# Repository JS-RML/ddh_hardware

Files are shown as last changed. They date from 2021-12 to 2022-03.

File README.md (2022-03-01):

# Direct-Drive Hand

In this project, we have implemented a two-fingered 4-DoF direct-drive hand, inspired by the work ["Direct Drive Hands: Force-Motion Transparency in Gripper Design"](http://www.roboticsproceedings.org/rss15/p53.pdf). 

ddh

# Table of Contents

- [Preparation](#preparation)
  - [Bill of Materials (BOM)](#bom)
    - [Off-the-Shelf Parts](#purchase)
    - [3D Printing](#3d-printing)
  - [Install `ddh_driver`](#install-ddh-driver)
  - [Labeling Parts](#labeling-parts)
- [Actuators](#actuators)
  - [Actuator Assembly ⨉4](#assemble-actuators)
  - [Wiring](#wiring)
    - [Power Supply](#power-supply)
    - [Encoder Connection](#encoder-connection)
    - [Power Connection](#power-connection)
  - [Actuator Calibration](#actuator-calibration)
    - [Calibrate ODrives](#calibrate-odrives)
    - [Calibrate Zero Position](#calibrate-zero-position)
- [Gripper](#Gripper)
  - [Finger Assembly ⨉2](#finger)
  - [Gripper Assembly](#gripper-assembly)
  - [Mounting](#mounting-ur10)
  - [Validation](#validation)
- [Customization](#customization)
  - [Mounting](#custom-mounting)
  - [Geometry](#geometry)
  - [Fingertip](#fingertip)
- [Getting Started](#getting-started)

# Preparation

## Bill of Materials (BOM)

### Off-the-Shelf Parts

- [ODrive 3.6-56V](https://odriverobotics.com/shop/odrive-v36) ⨉2
- [T-Motor GB54-2](https://store.tmotor.com/goods.php?id=445) ⨉4
- [AS5048A Encoder + Diametrical Magenet](https://item.taobao.com/item.htm?id=619004953504) ⨉4
- [Bearing - outer-diameter = 10mm, inner-diameter = 6mm](https://item.taobao.com/item.htm?id=649671875461) ⨉12
- [Dowel Pin - diameter = 6mm, length = 10mm](https://detail.tmall.com/item.htm?id=522002486638) ⨉6
- [14-Core Shielded Cable TRVVSP4](https://detail.tmall.com/item.htm?id=649477061772) ⨉2 meters
- [MX1.25-6P 150mm Cable](https://item.taobao.com/item.htm?id=607231799768) ⨉4
- [AMASS Braided 3-Phase 90cm Cable](https://item.taobao.com/item.htm?id=520248392055) ⨉8
- Adapter Plate and Coupling: The gripper is primarily designed to be compatible with [Universal Robots UR10](https://www.universal-robots.com/products/ur10-robot/) (50mm PCD with 4 ⨉ M6, used with Robotiq's grippers). For other robot systems, see the section [Customization](#custom-mounting) for instructions.
- Various Fasteners from M2 to M4

### 3D Printing 

- [Magnet Holder](stl/magnet_holder.STL) ⨉4
- [Motor Plate](stl/motor_plate.STL) ⨉4
- [Proximal Link](stl/proximal_link.STL) ⨉4
- [Distal Link](stl/distal_link.STL) ⨉2
- [Distal Tip Link](stl/distal_tip_link.STL) ⨉2
- [Finger Tip](stl/finger_tip.STL) ⨉2
- [Gripper Shell](stl/gripper_shell.STL) ⨉1
- [Coupler](stl/coupler.STL) ⨉1
- [Calibration Stand](stl/calibration_stand.STL) ⨉4
- [Calibration Arm](stl/calibration_arm.STL) ⨉4

## Install `ddh_driver`

`ddh_driver` is our driver software that provides a user interface to the gripper hardware. To install, visit [here](https://github.com/HKUST-RML/ddh_driver).

## Labeling Parts

Labeling parts can facilitate assembly.

### Motors

Label the four motors with `R0`, `R1`, `L0`, `L1`, respectively. The motors will __not__ be interchangeable later.

### ODrive

Label the two ODrive boards with `ODrive_R` and `ODrive_L` respectively. Record their serial numbers in `ddh_driver/config/default.yaml`. You can check the serial number using `odrivetool` in the terminal.

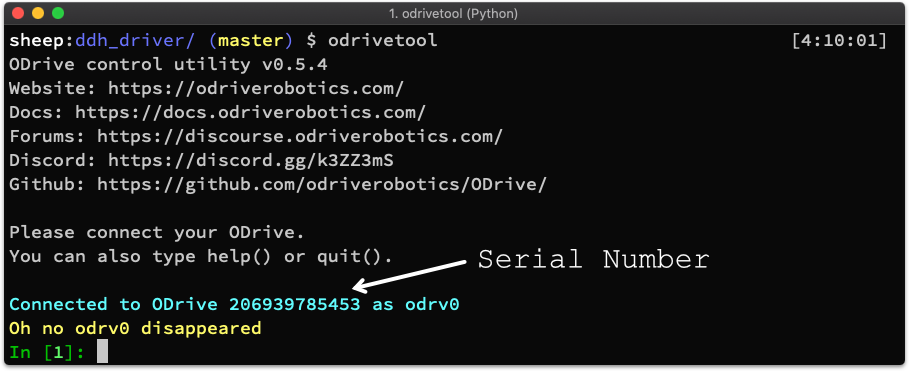
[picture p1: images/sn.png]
sn


```yaml
odrive_serial:
  R: 'Serial Number of ODrive_R'
  L: 'Serial Number of Odrive_L'
```

### Gripper Shell

On one side of the 3D-printed part `Gripper Shell` (to be used as the top side), mark reference frames as follows.

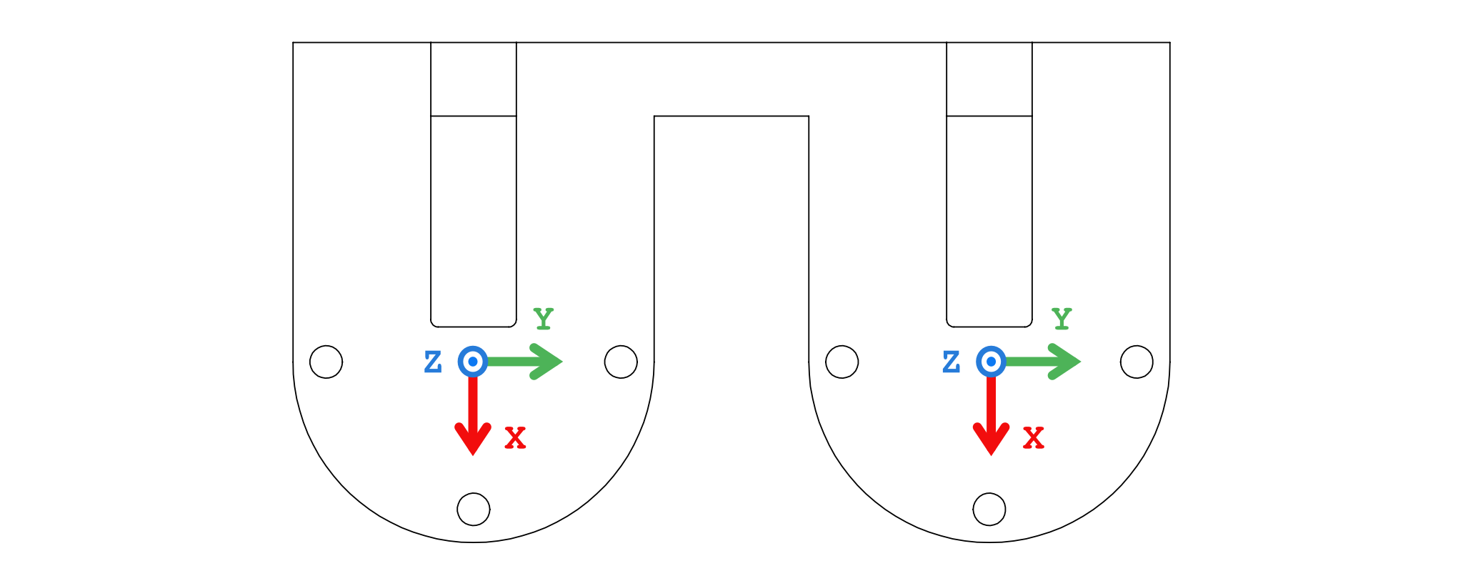
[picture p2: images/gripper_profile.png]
ref_frame


# Actuators

Actuator = BLDC Motor + Magnet + Encoder + Drive Board

## Actuator Assembly ⨉ 4

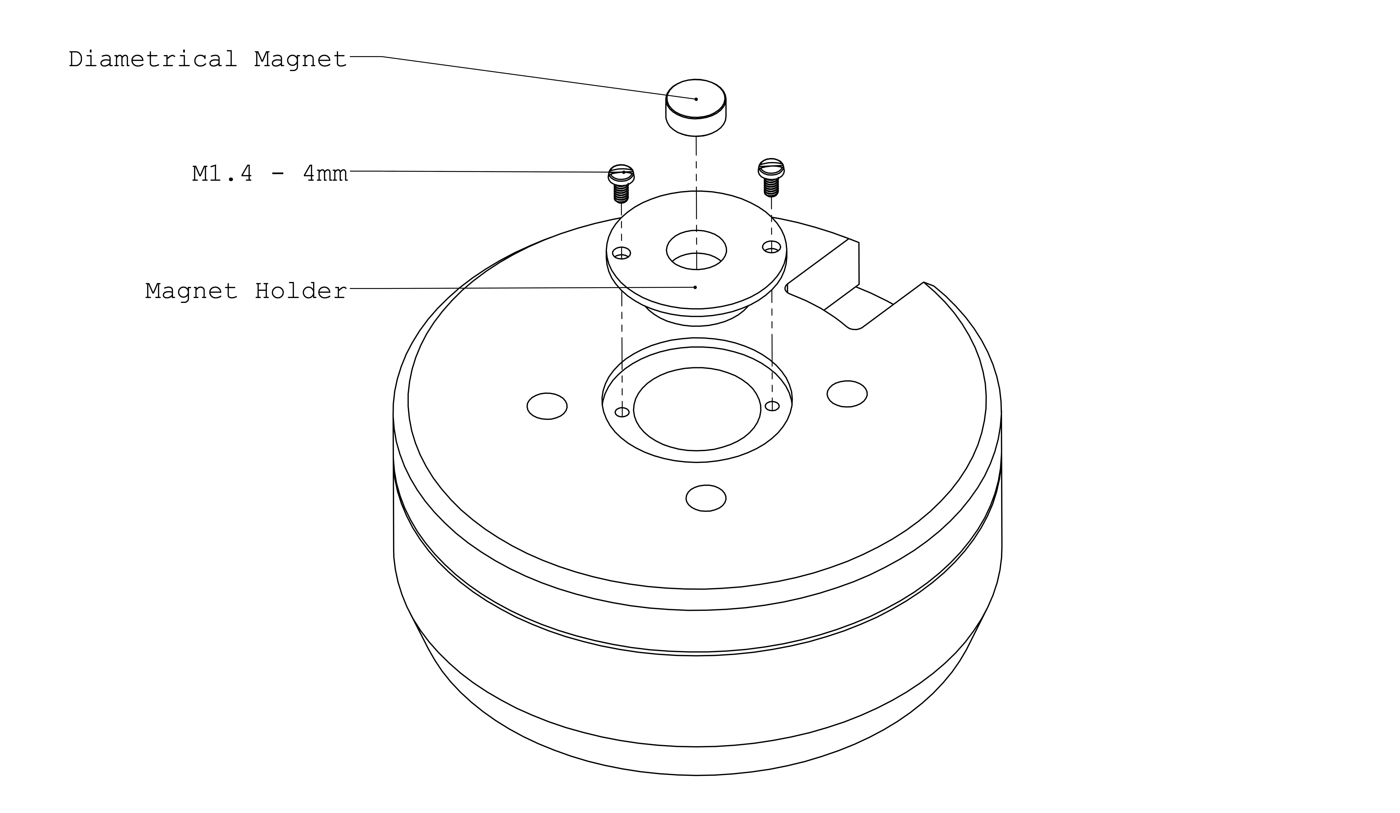
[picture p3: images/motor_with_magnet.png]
motor_with_magnet


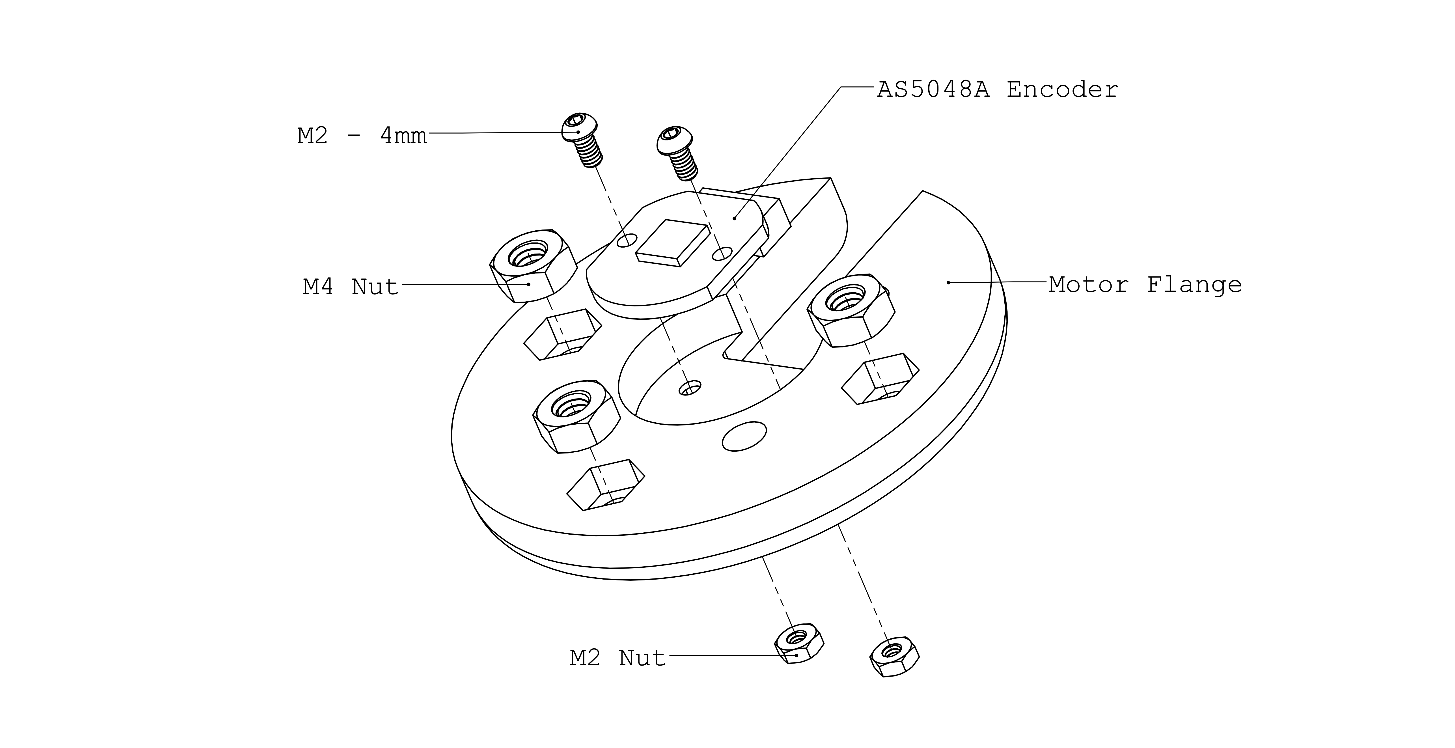
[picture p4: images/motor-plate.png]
motor-plate


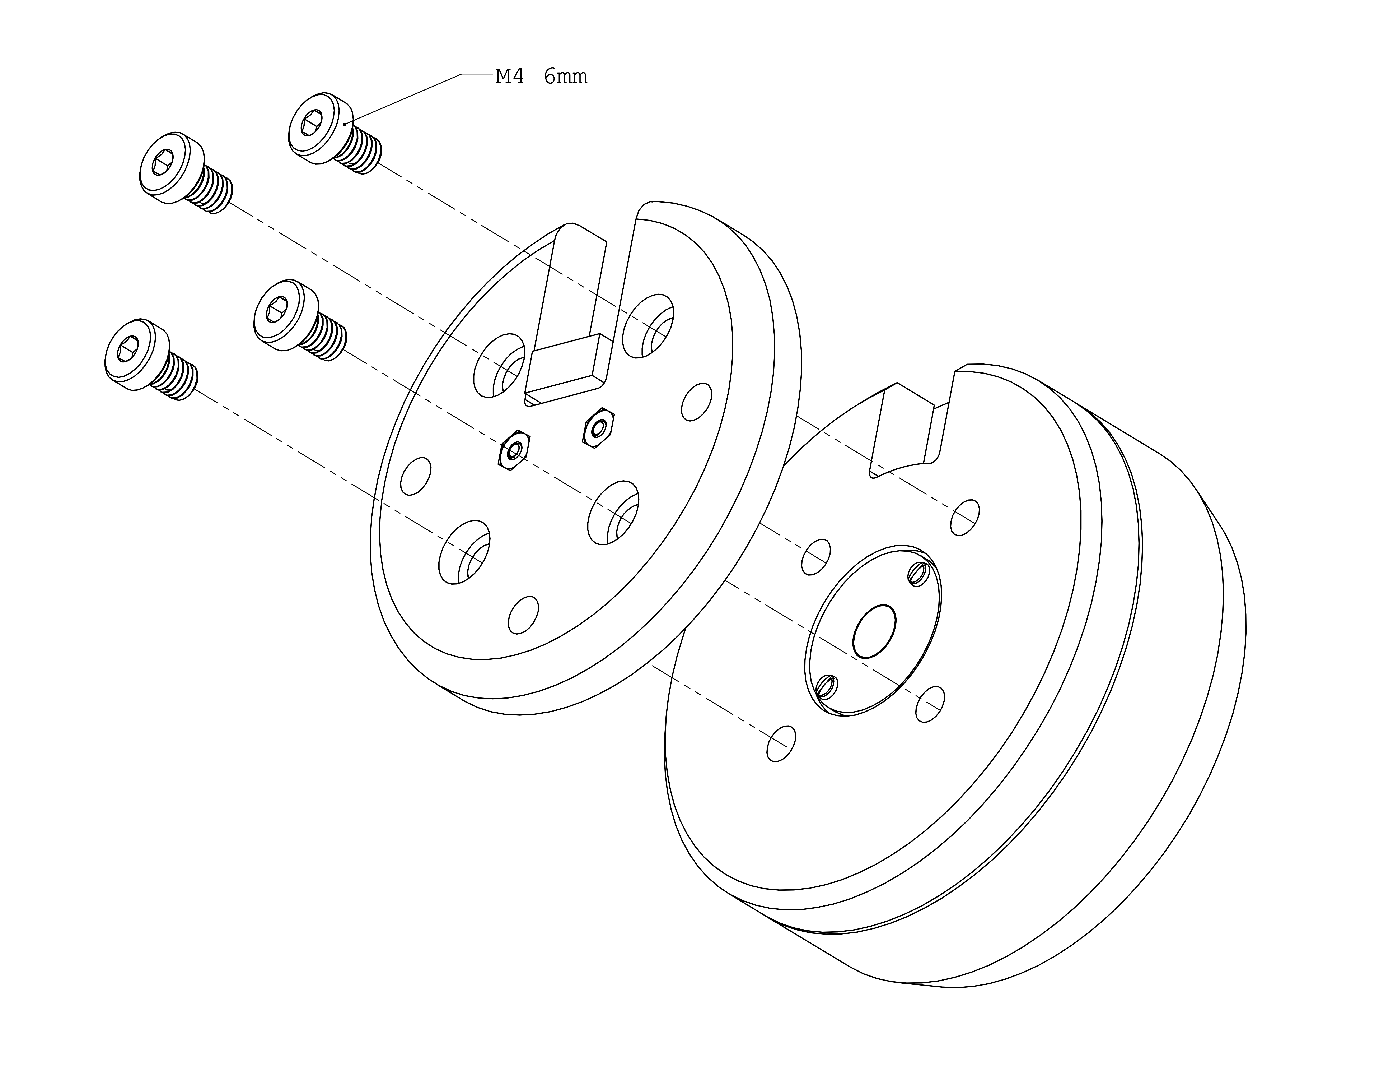
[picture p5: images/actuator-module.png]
actuator_module


## Wiring

The components should be connected following the diagram below. The encoder connection (black) and power connection (green) will be further elaborated.

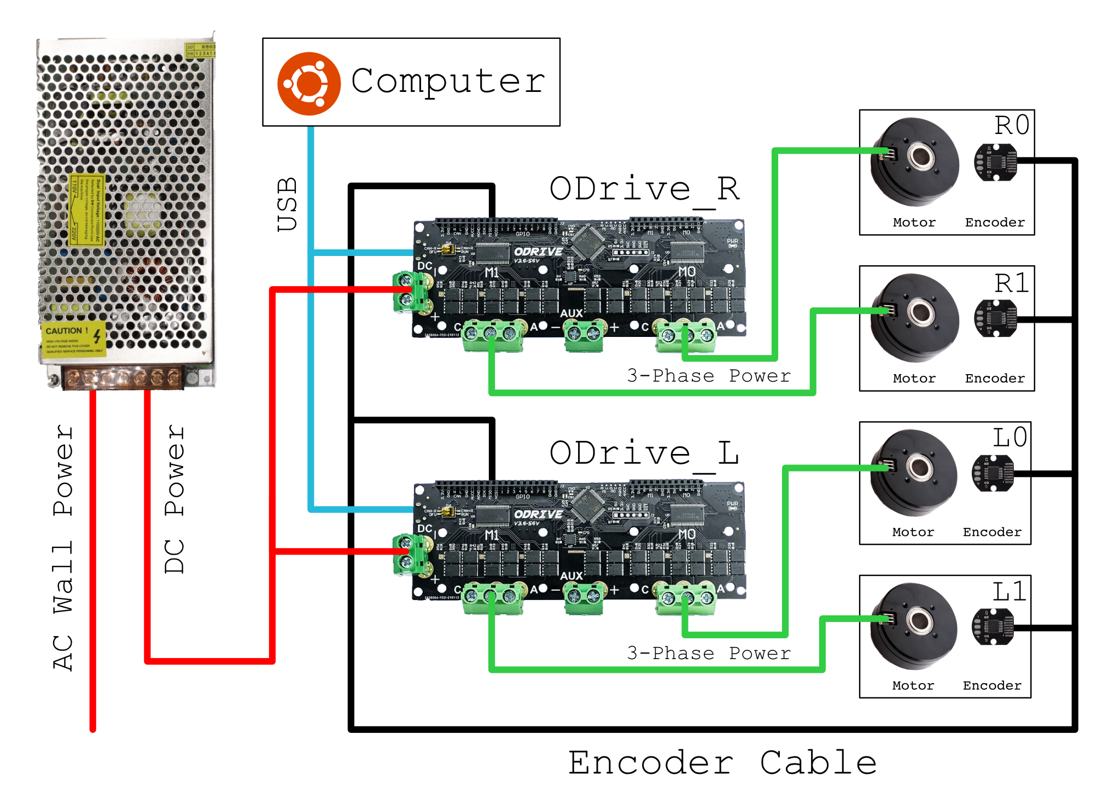
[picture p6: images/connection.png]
connection


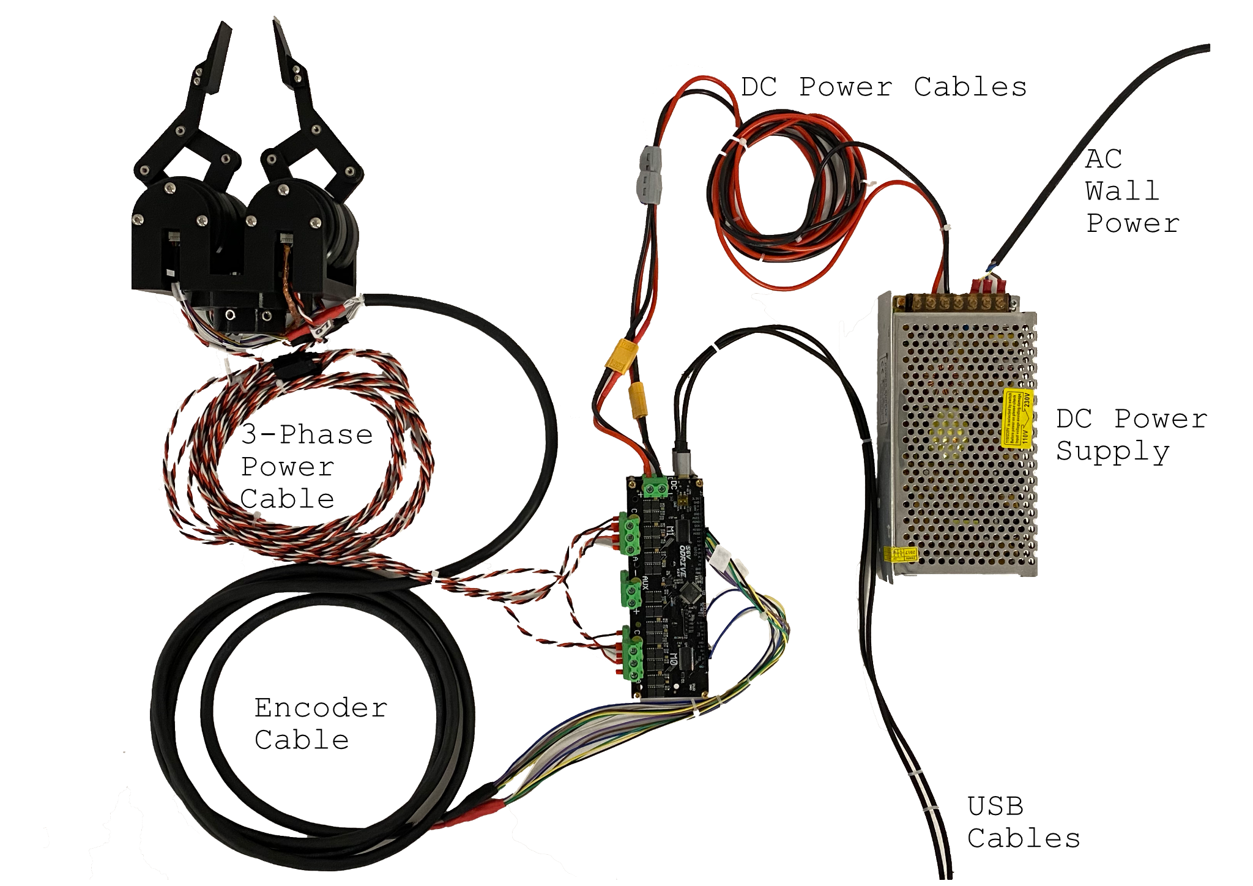
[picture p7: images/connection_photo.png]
connection_real


### Power Supply

First connect the DC power supply to the wall plug. The __brown__, __blue__, and __yellow__ wires correspond to __L__, __N__ and __Ground__ ports on the power supply. Then connect it to the two ODrive boards, positive to positive, negative to negative. There is no on/off button, plug in the wall plug to turn the system on, unplug to turn it off. Power it on does not arm the motors.

### Encoder Connection

For the encoder connection, we fabricate a cable assembly as shown below in the schematic. It is recommended to verify the connectivity and resistance of each connection to make sure the cables are soldered properly. We also recommend to label each connector like the schematic.

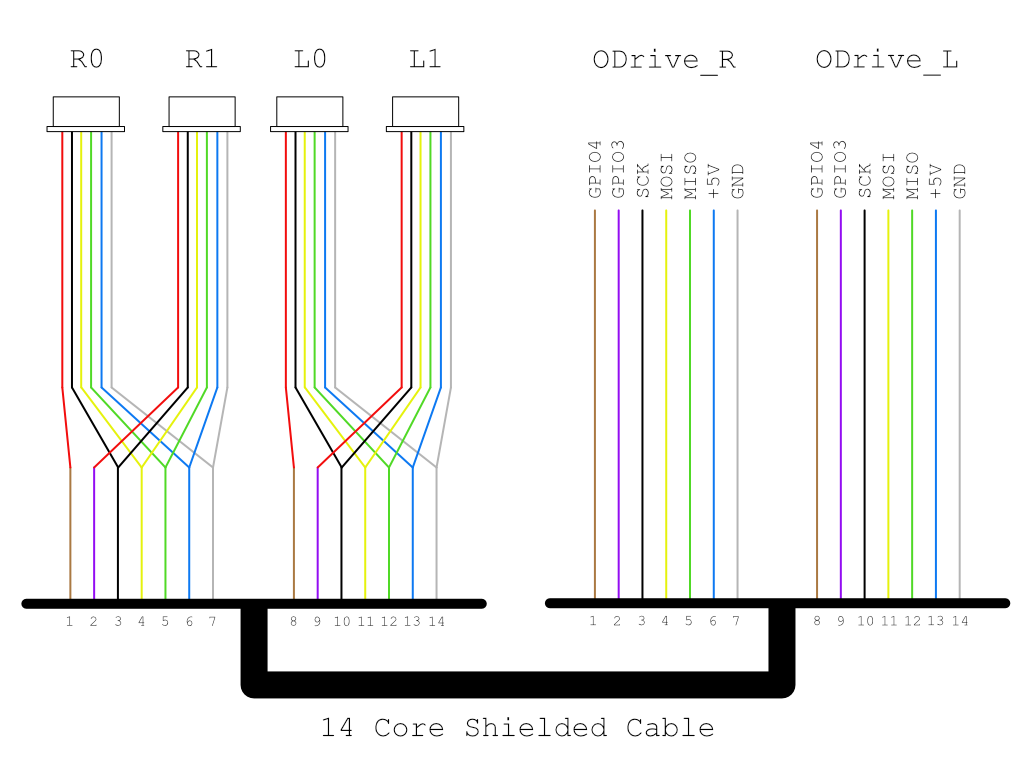
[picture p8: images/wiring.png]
drag_cable


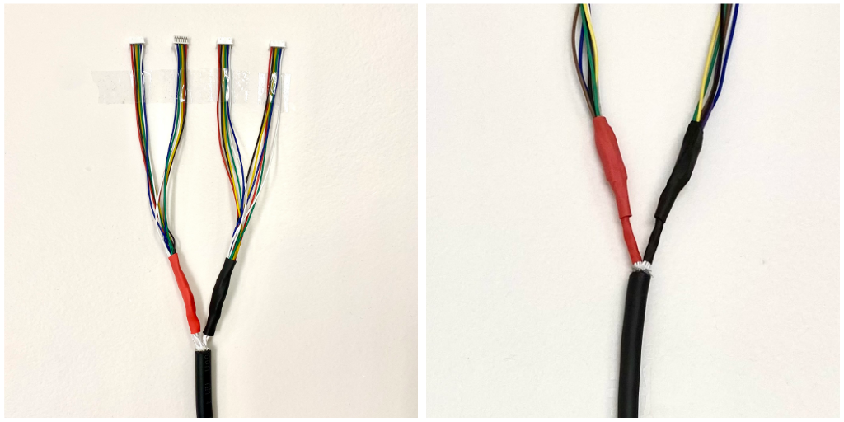
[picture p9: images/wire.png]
wire


After successful fabrication, connect the motor encoders and the ODrives.

### Power Connection

For the power connection, the motors are matched with the ODrive axes as follows: 

| Actuator | ODrive | Axis |
|----|---|-----|
| R0 | ODrive_R | M0 |
| R1 | ODrive_R | M1 |
| L0 | ODrive_L | M0 |
| L1 | ODrive_L | M1 |

Keep the 3-phase connection consistent as shown below. 

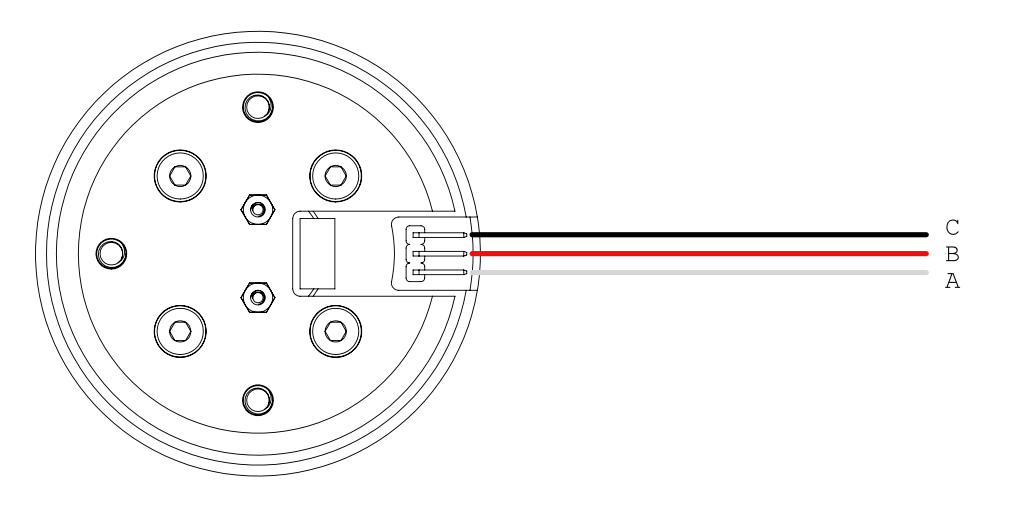
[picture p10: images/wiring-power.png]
wireing_power


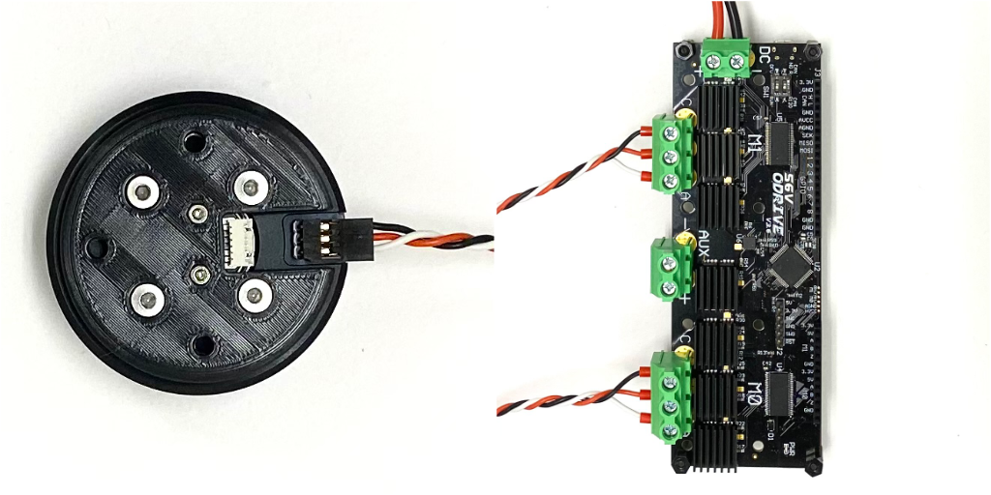
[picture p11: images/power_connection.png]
power-connection


## Actuator Calibration

Each actuator module require calibration before use. This step __can not__ be done after the gripper is assembled, so do not postpone this step.

We explicitly define the `direction of the rotor` to be the direction the hexagonal logo on the rotor is pointing at, and the `zero position of the motor` to be when the direction of the motor is pointing at the opposite direction of the power port on the stator. 

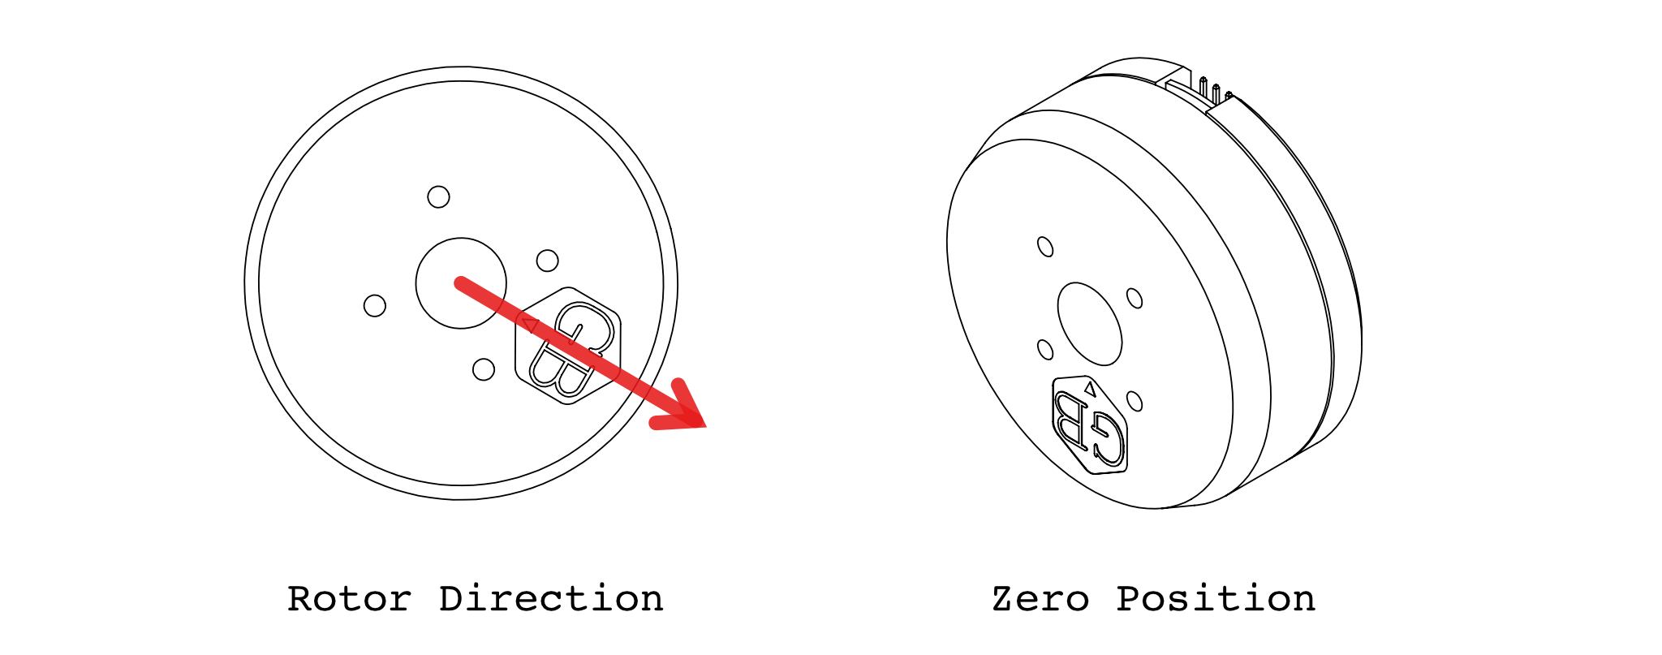
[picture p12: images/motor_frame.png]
motor-zero


### Calibrate ODrives

Execute the following command and follow its instructions in the terminal.

```shell
python3 -m ddh_driver.calib_odrive
```

### Calibrate Zero Position

Here we calibrate the zero position of the motor. Mount the actuator on the calibration stand and install the calibration arm onto the actuator according to the diagram

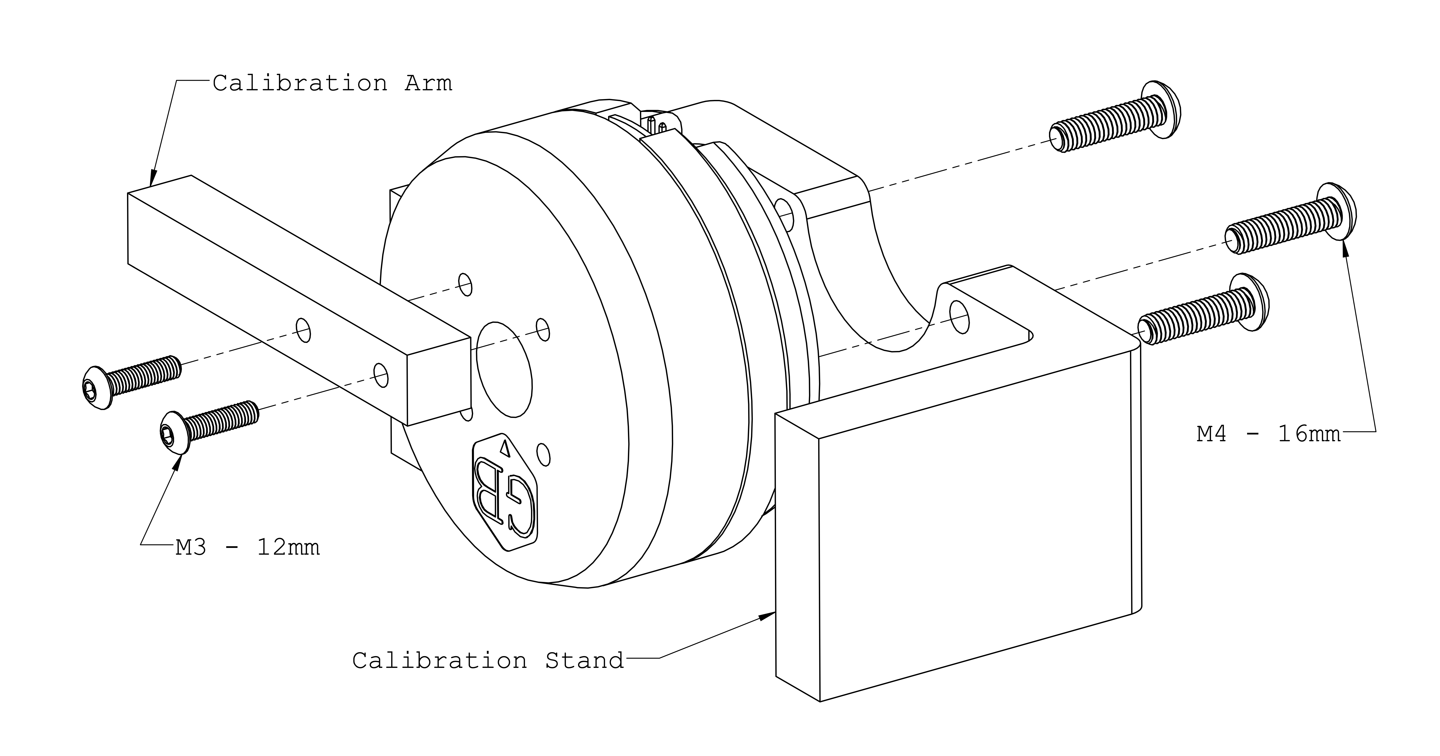
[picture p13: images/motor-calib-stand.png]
calibration-stand


Execute the following command to show real-time reading from the encoders.
```shell
python3 -m ddh_driver.check_encoder
```

Put the motor into zero position as show in the diagram below. Press down the calibration arm to make sure the stand and arm touch tightly. 

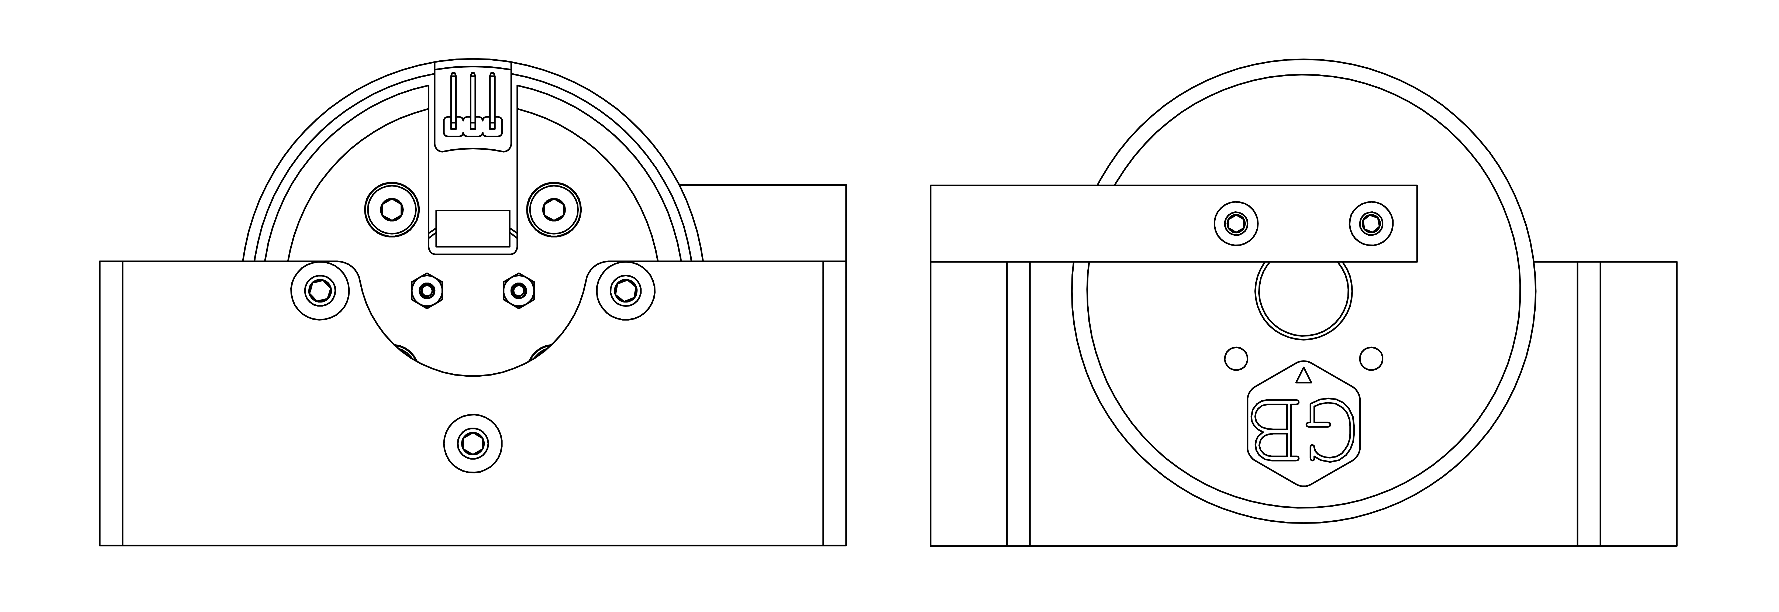
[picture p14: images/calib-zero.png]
zero-stop


Record the encoder reading in configuration in `ddh_driver/config/default.yaml`. Perform this calibration for each actuator and record it in their respective keys in the configuration file.
```yaml
motors:
  R0: # and R1, L0, L1:
    offset: the encoder reading at zero stop
```

After modifying the configuration file, execute the following command will show the real-time reading of the motor angular position in degrees.
```shell
python3 -m ddh_driver.check_motor_pos
```
It should be zero when motor is in [zero position](#zero-position-of-the-motor). Also try 90° and 180°. Don't mind the sign at this stage of assembly.

# Gripper

## Finger Assembly ⨉ 2

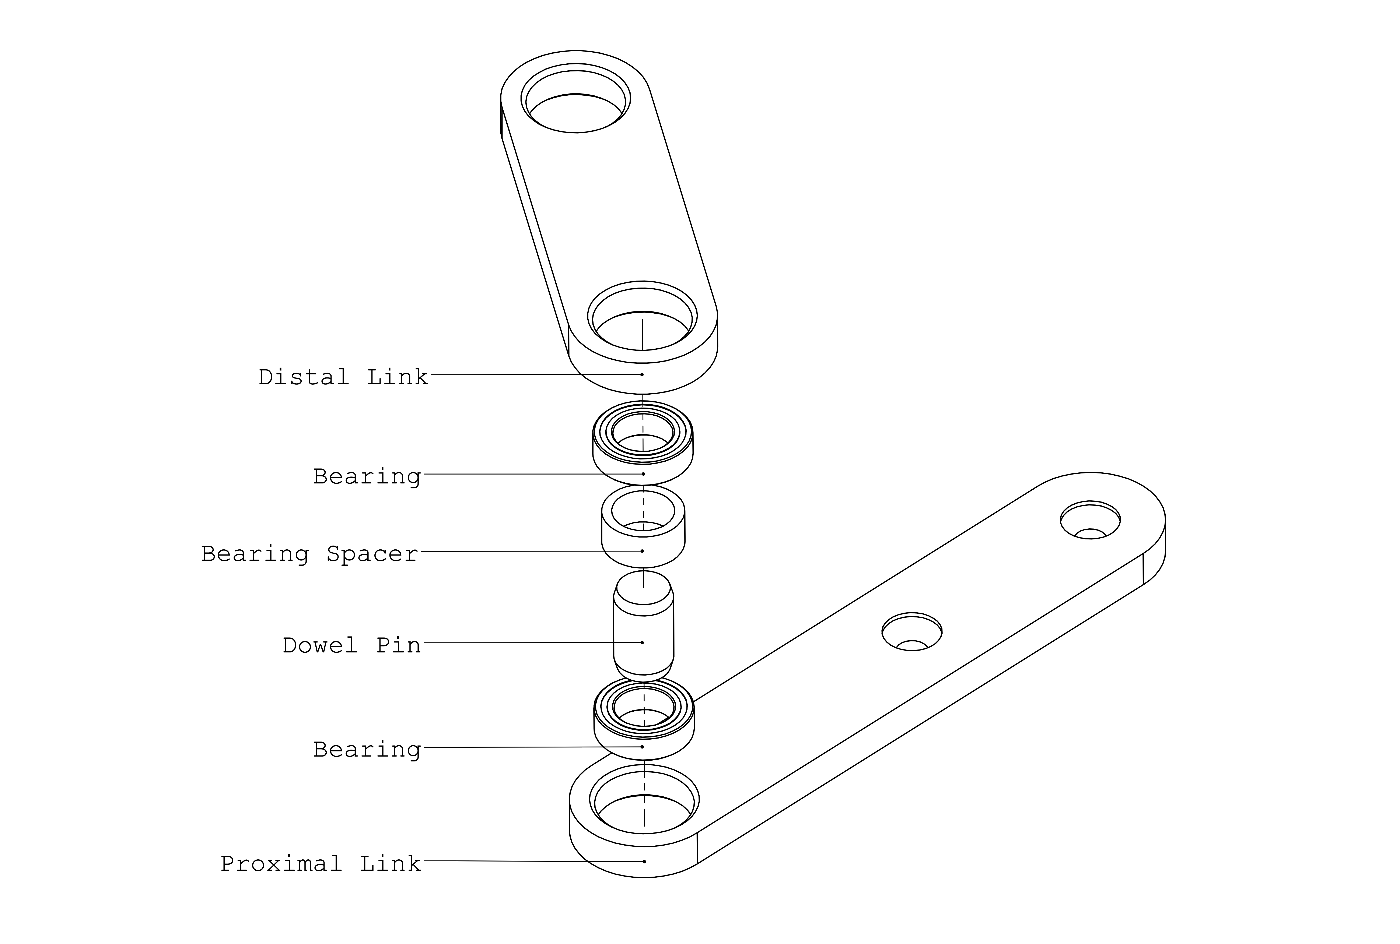
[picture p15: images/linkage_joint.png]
linkage_joint


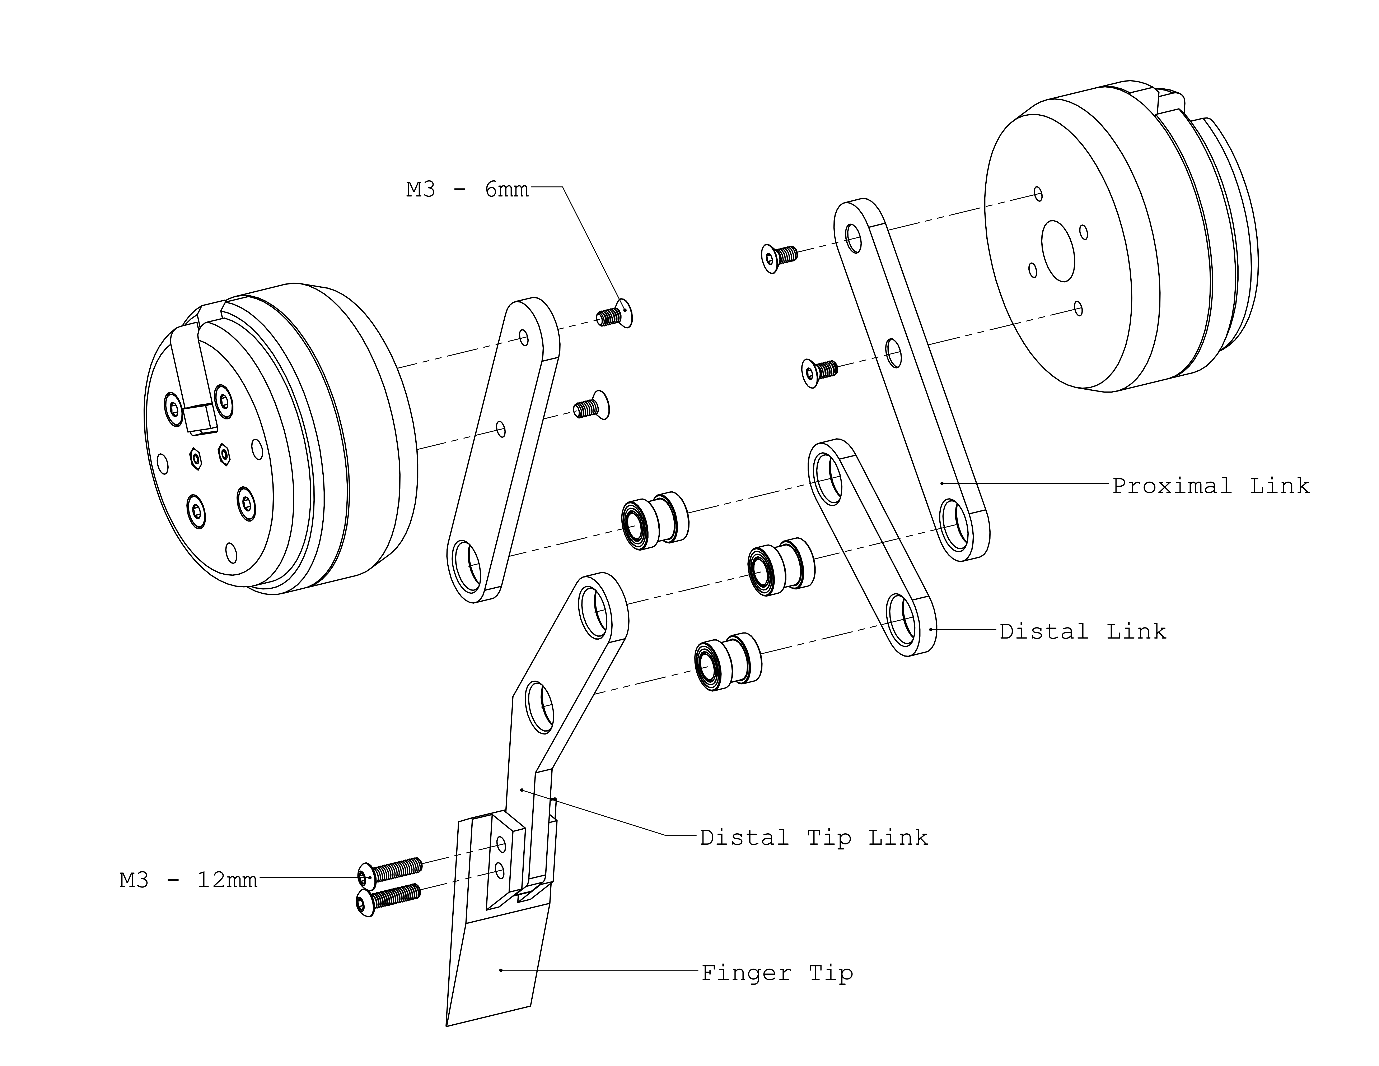
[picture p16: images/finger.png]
finger


## Gripper Assembly

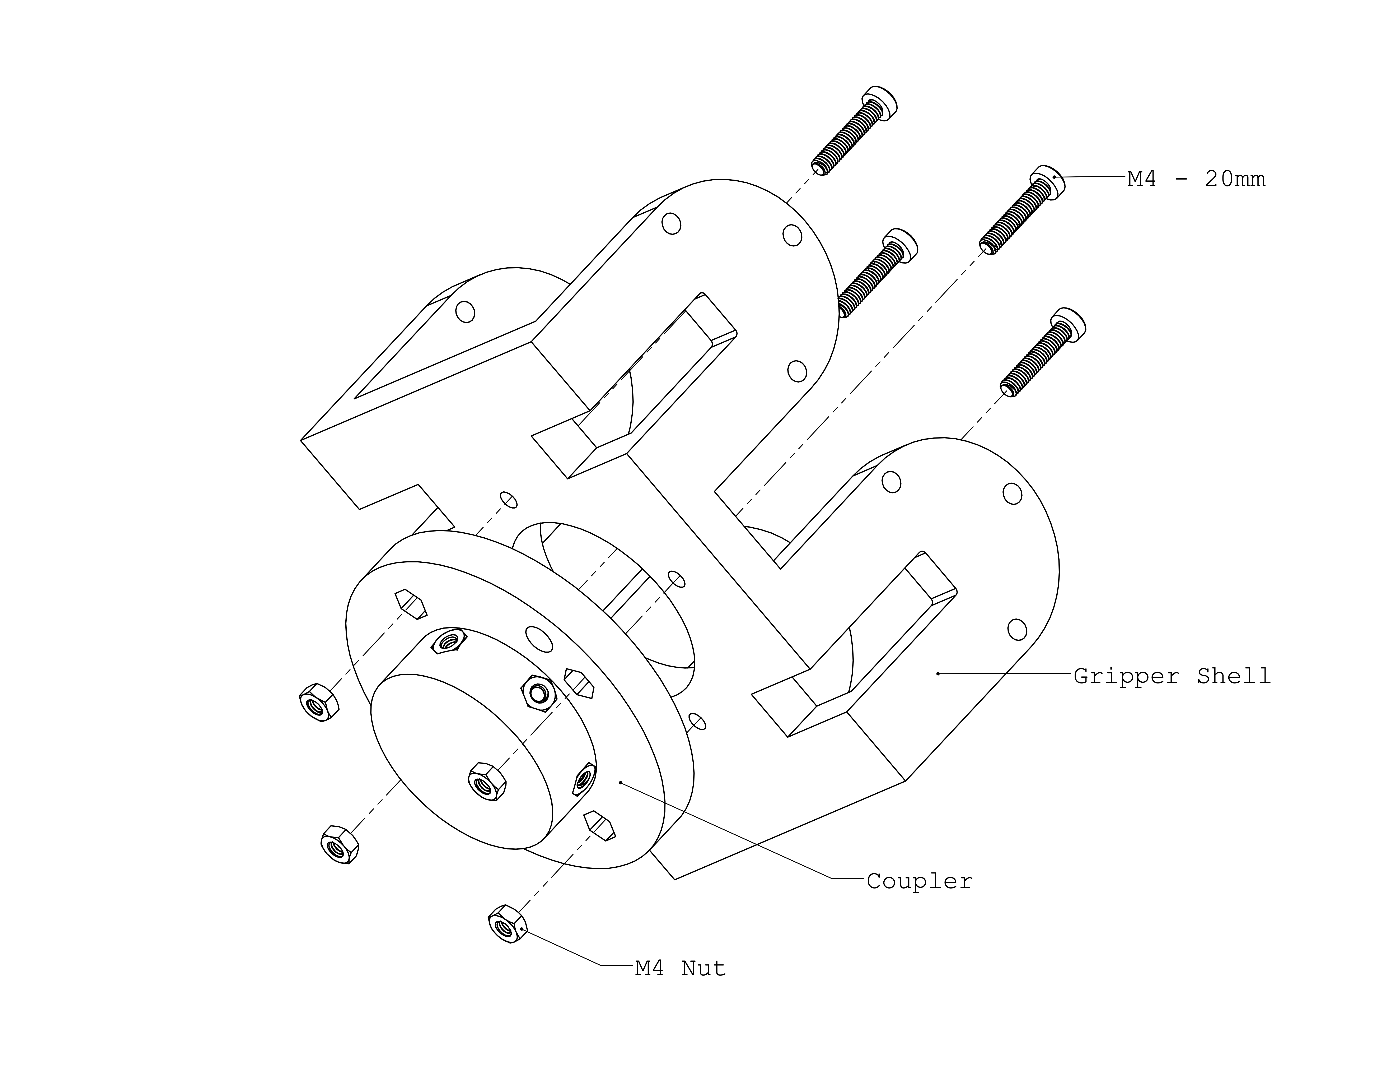
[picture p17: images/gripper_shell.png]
gripper_shell


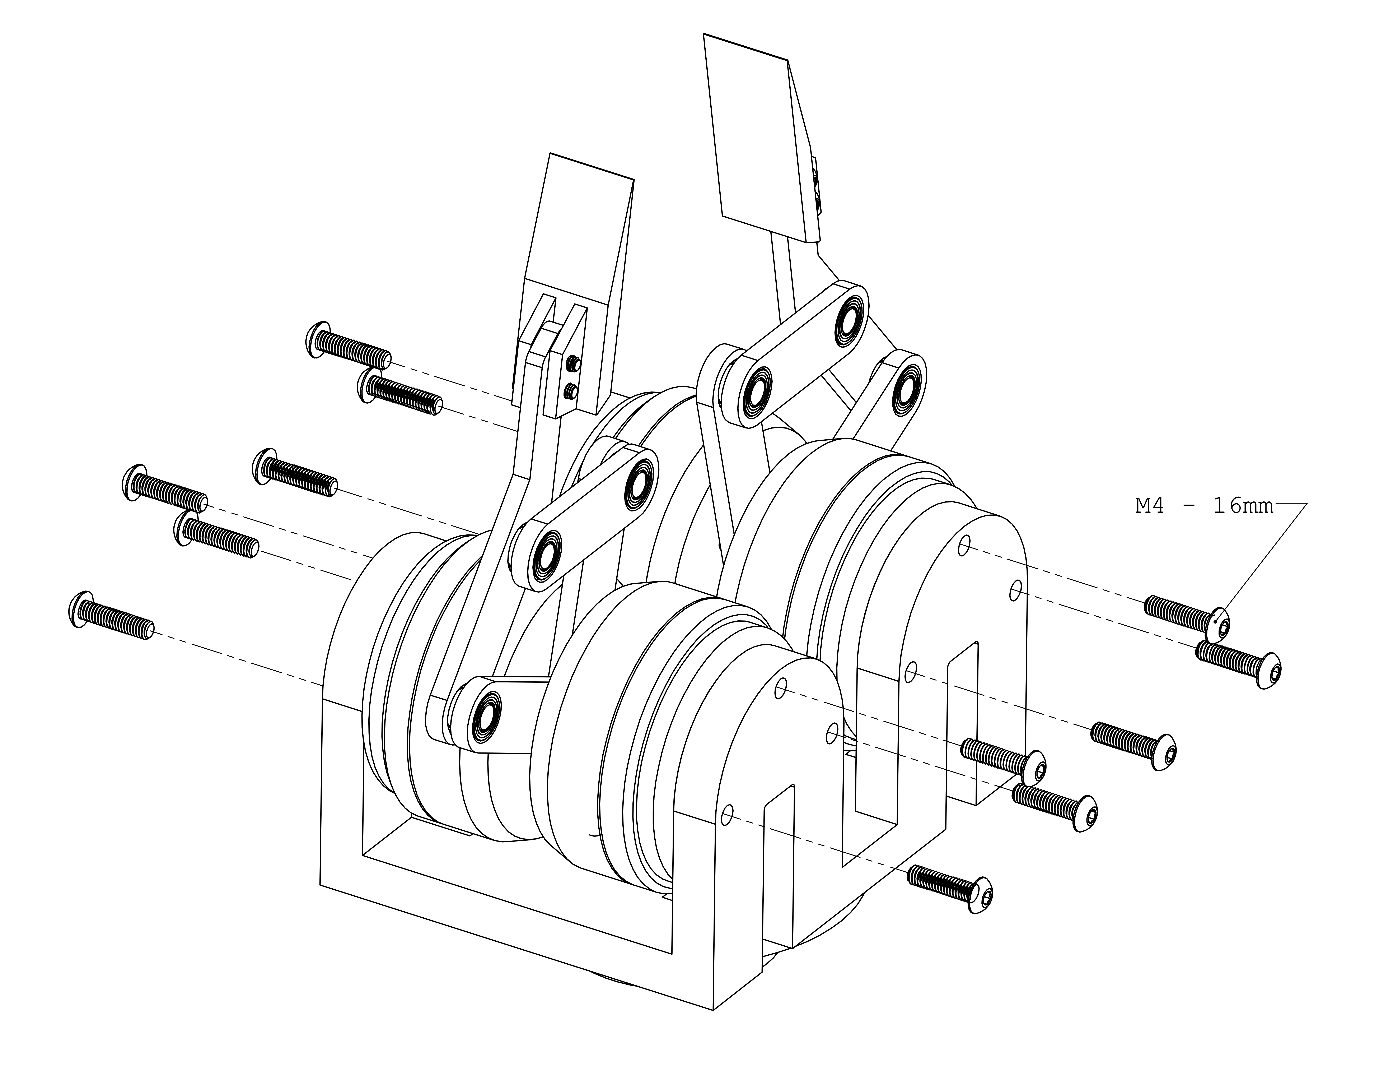
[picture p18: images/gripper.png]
gripper


## Mounting

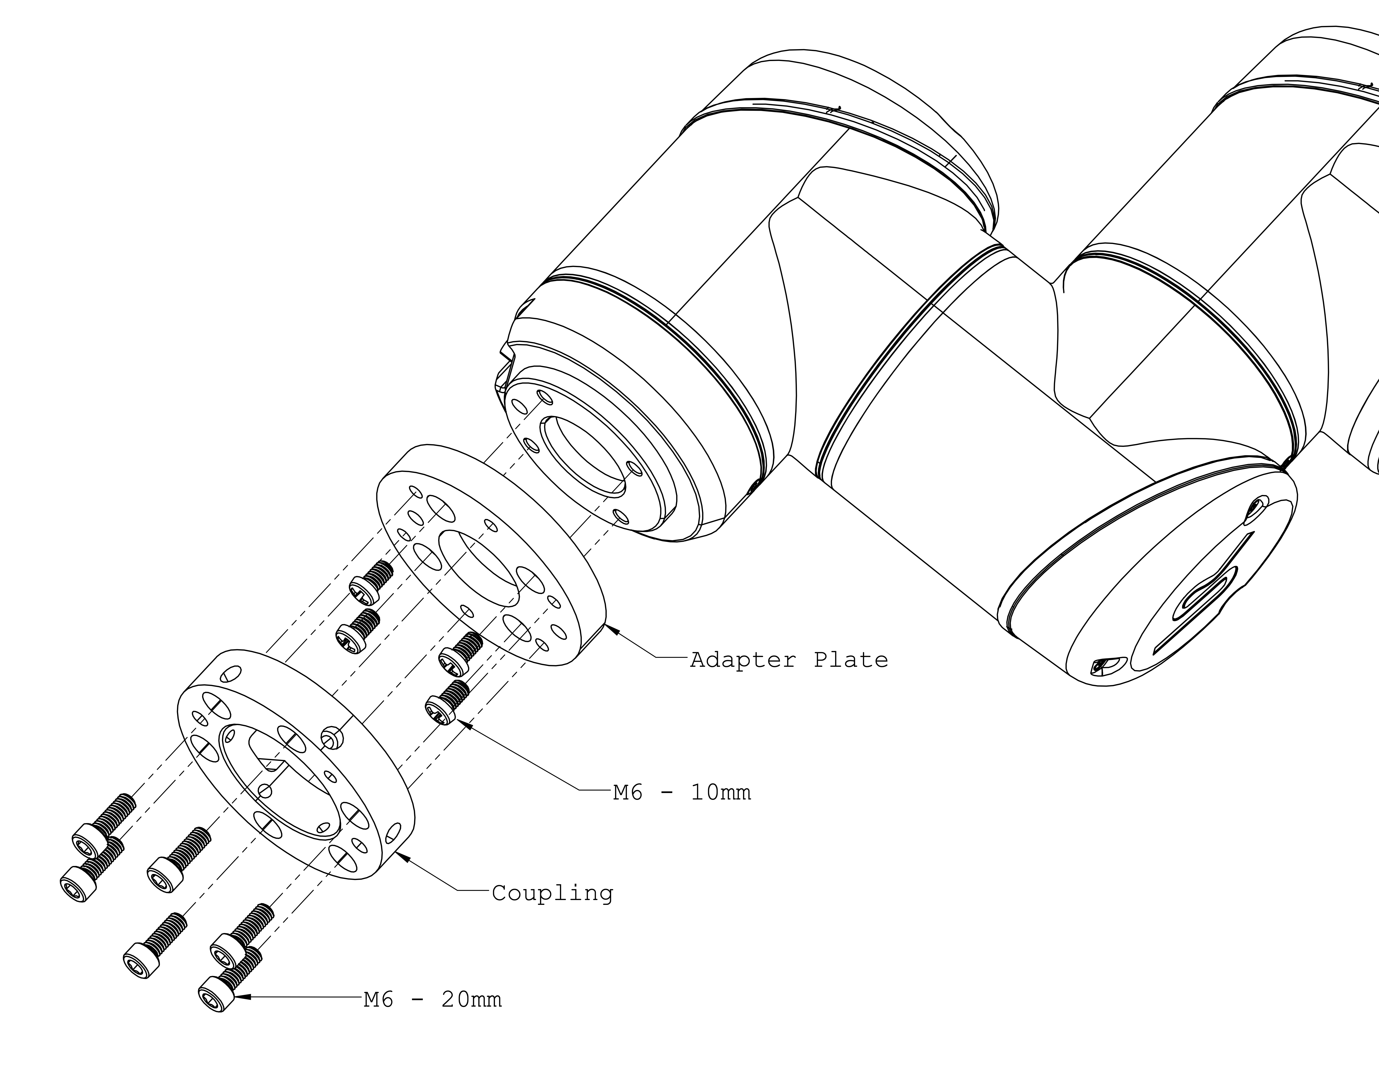
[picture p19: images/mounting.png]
mounting


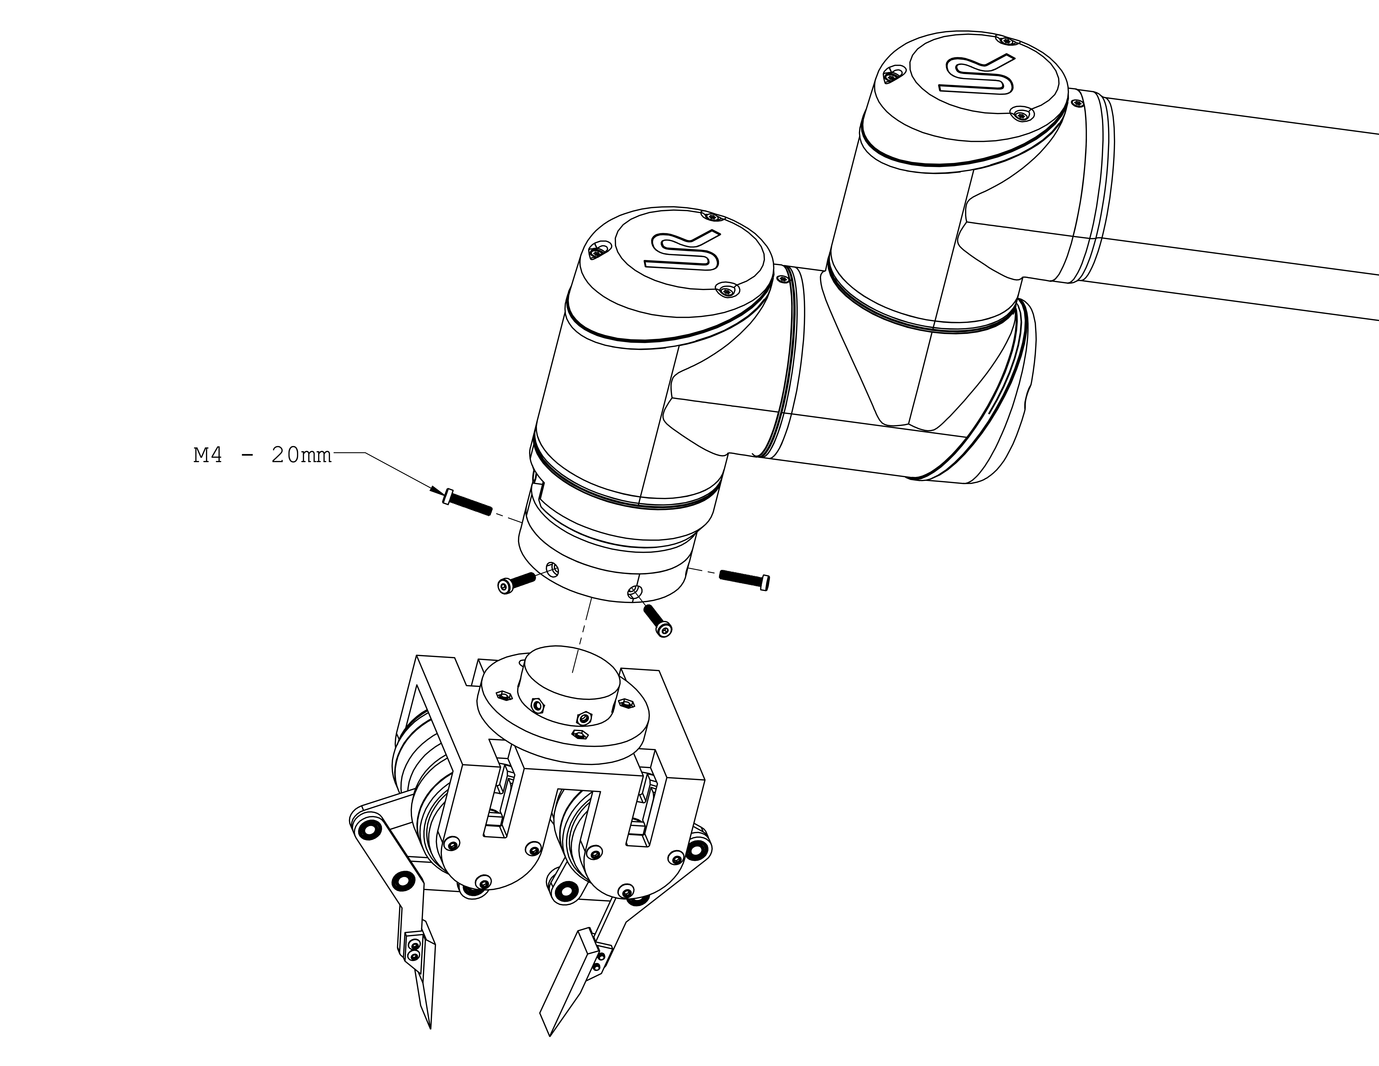
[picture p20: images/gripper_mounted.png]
gripper_mounted


## Validation

The gripper assembly is complete. Please perform the following validation steps to make sure the linkages and actuators are installed correctly.

First check the association between proximal links and actuators. They should follow the diagram below __exactly__. If there is a mismatch, please go back to the assembly steps and correct the mistakes.

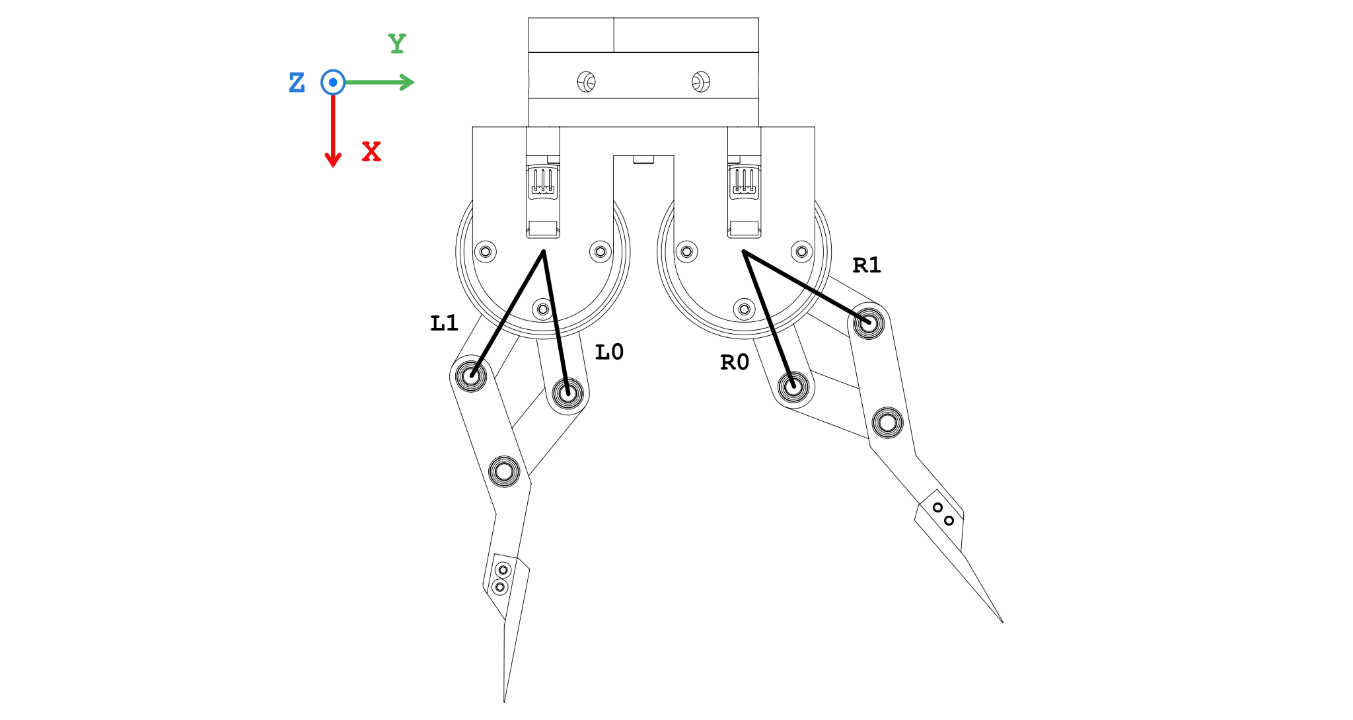
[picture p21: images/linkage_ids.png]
linkage_ids


Then check the angular position of the four proximal links. This value will be referred to as θ, with subscript indicating which link.  Execute the following command to print real-time reading of θ
```shell
python3 -m ddh_driver.check_theta
```
It should be the angle between the link and the x-axis, in counter-clockwise direction. For example, the following figure shows the angle of R0 link at -40°, 0°,  and 90°.
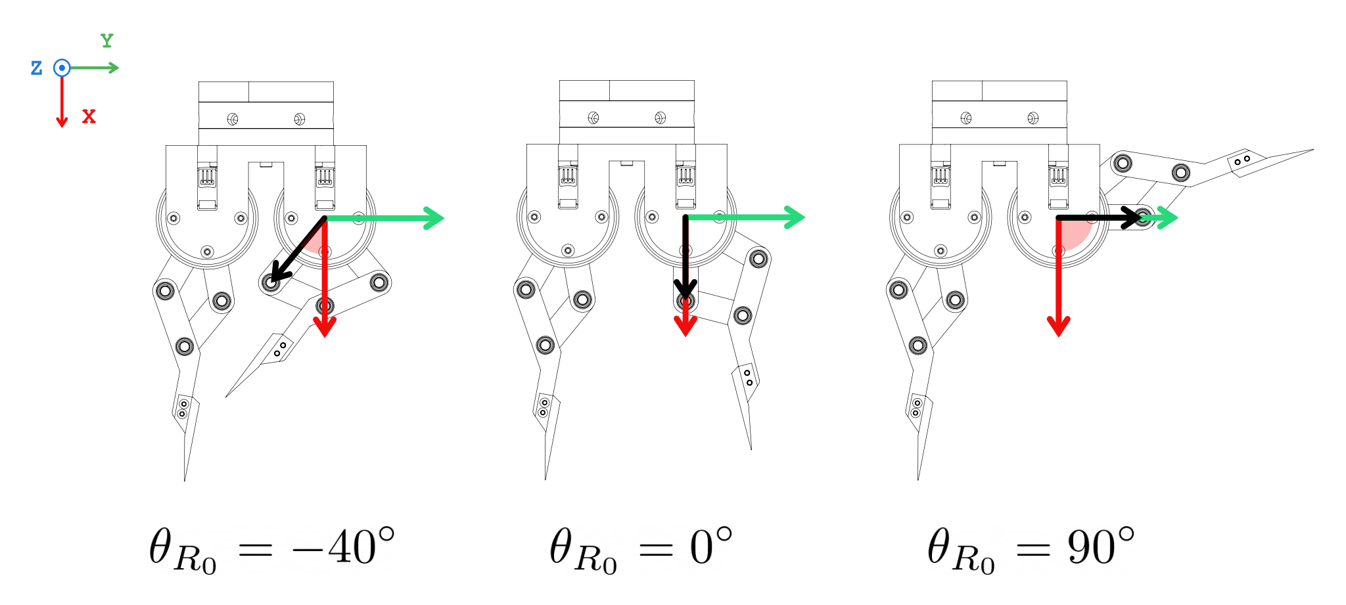
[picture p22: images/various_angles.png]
various-angles

If everything checked out at this point, you have successfully built and calibrated the direct-drive gripper.

# Customization

If the default setup does not satisfy your requirements, it can be further customized.

## Mounting

If the default mounting does not work for you, it's very easy to make a custom mount. The gripper has a __60 mm PCD with 4 ⨉ M4__ mounting interface, as shown in the drawing below.

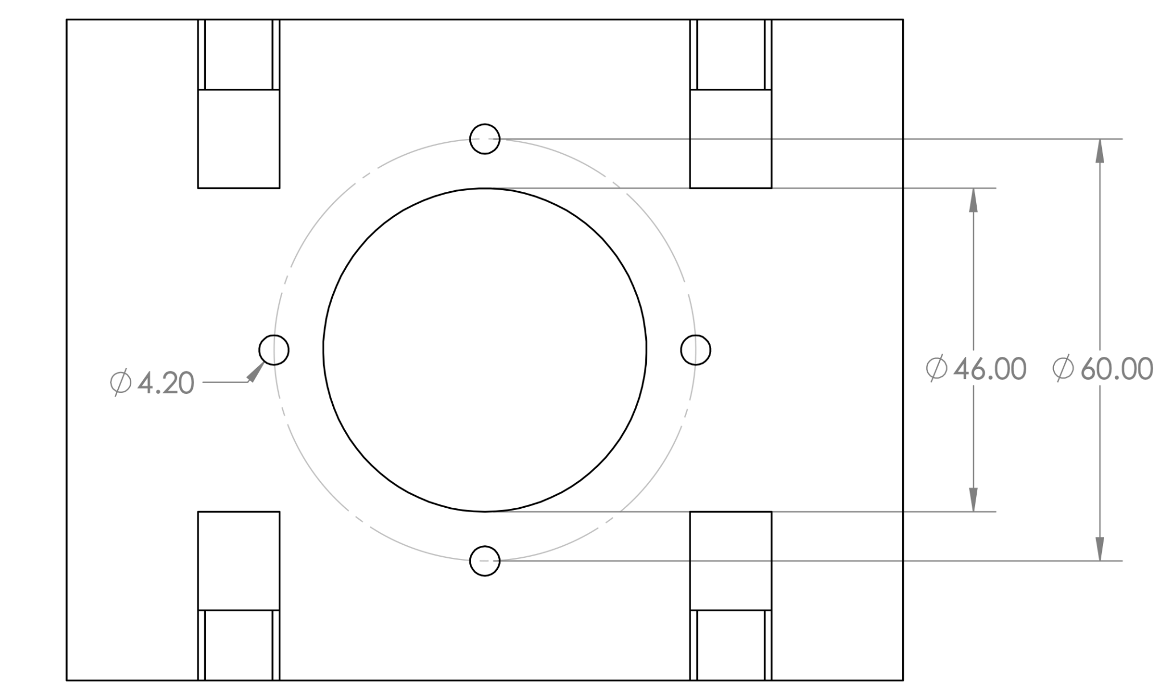
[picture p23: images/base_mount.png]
base_mount


## Geometry

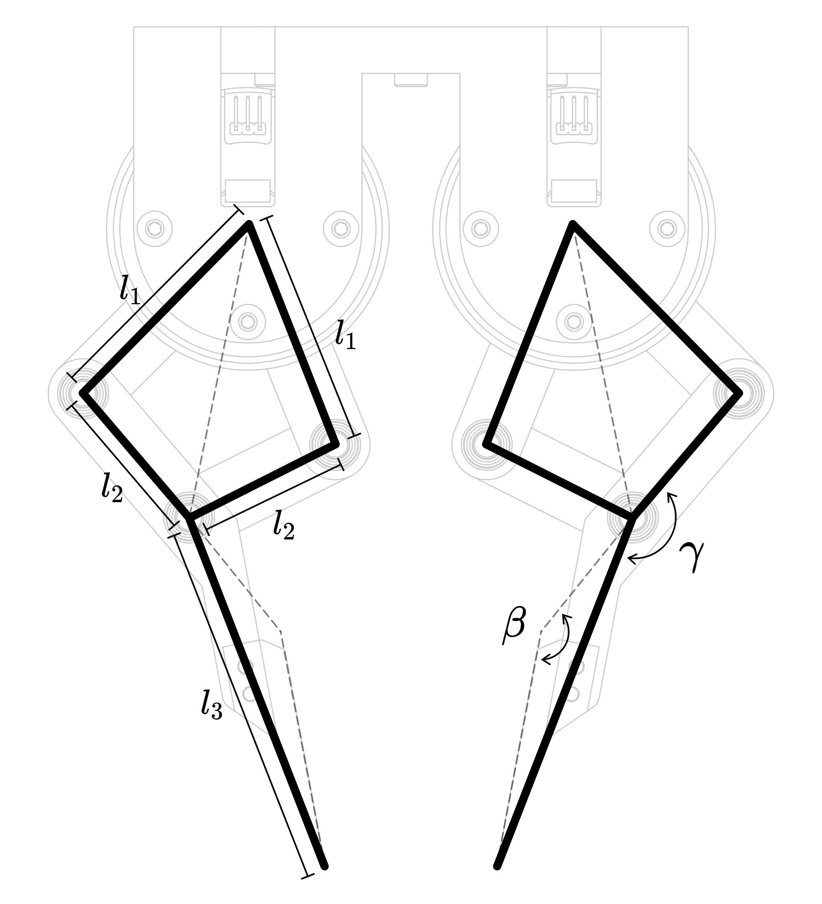
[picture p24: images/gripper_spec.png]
geometry


The geometrical parameters can be customized. After you design your custom parts, update the `ddh_driver/config/default.yaml` so the driver can work properly. 

| Parameter | Configuration Path | Unit |
|----|---|-----|
| ℓ₁ | `/geometry/l1` | mm |
| ℓ₂ | `/geometry/l2` | mm |
| ℓ₃ | `/geometry/l3` | mm |
| 𝝱 | `/geometry/beta` | degree |
| 𝛄 | `/geometry/gamma` | degree |

## Fingertip

The fingertip is designed to be swappable. It is attached to the distal link, shown in the schematic below. The default fingertip has a sharp tip for scooping thin objects. Customize the fingertip for your specific scenario. Beware that ℓ₃ and 𝝱 change with the fingertip geometry, make sure to update them in the configuration file.

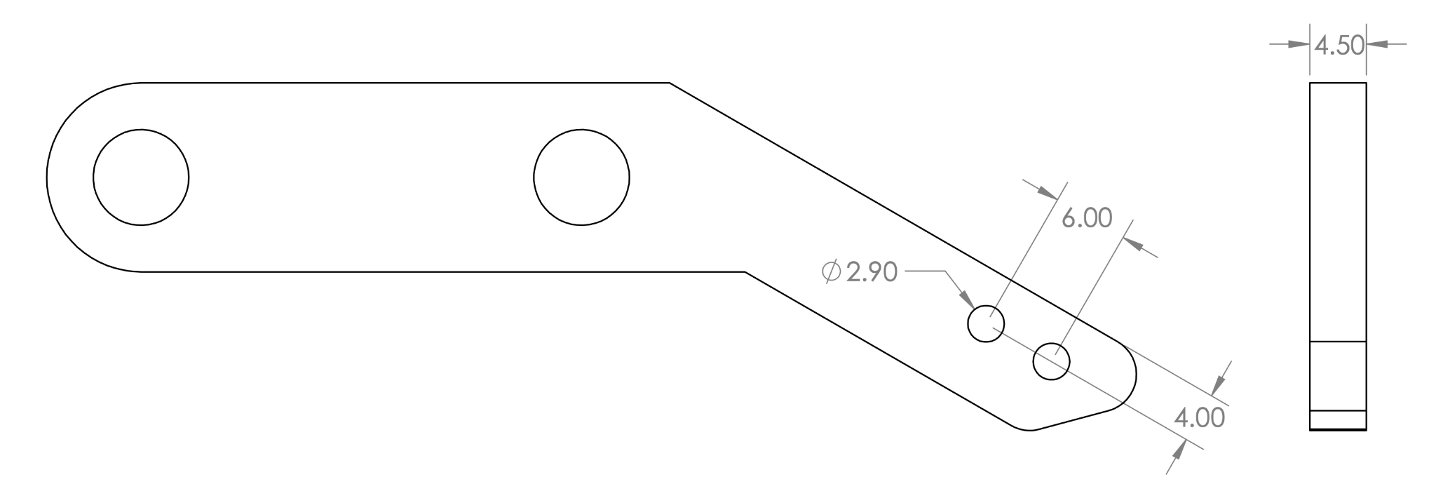
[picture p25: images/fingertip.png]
fingertip


# Getting Started

You have completed the assembly and calibration of the direct-drive gripper. To learn about how to use the gripper, please proceed to the [ddh_driver](https://github.com/HKUST-RML/ddh_driver) for tutorials and documentation.

# Maintenance

For any technical issues, please contact Pu Xu ([pxuaf@connect.ust.hk](mailto:pxuaf@connect.ust.hk))

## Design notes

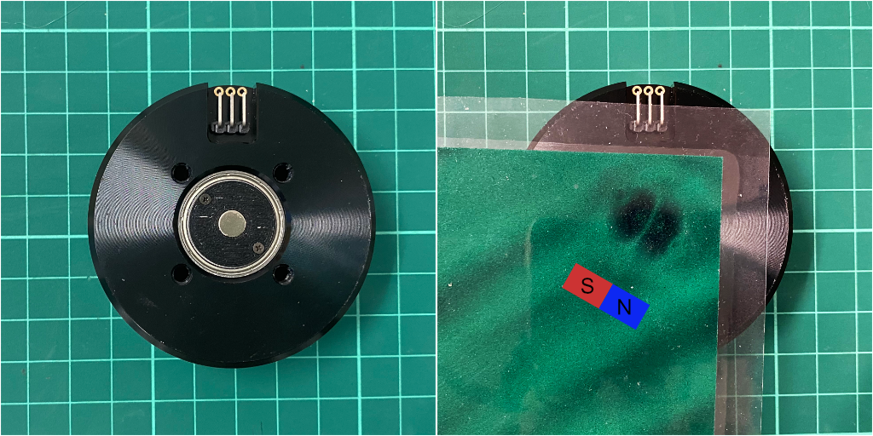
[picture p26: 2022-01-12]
images/magnet.png

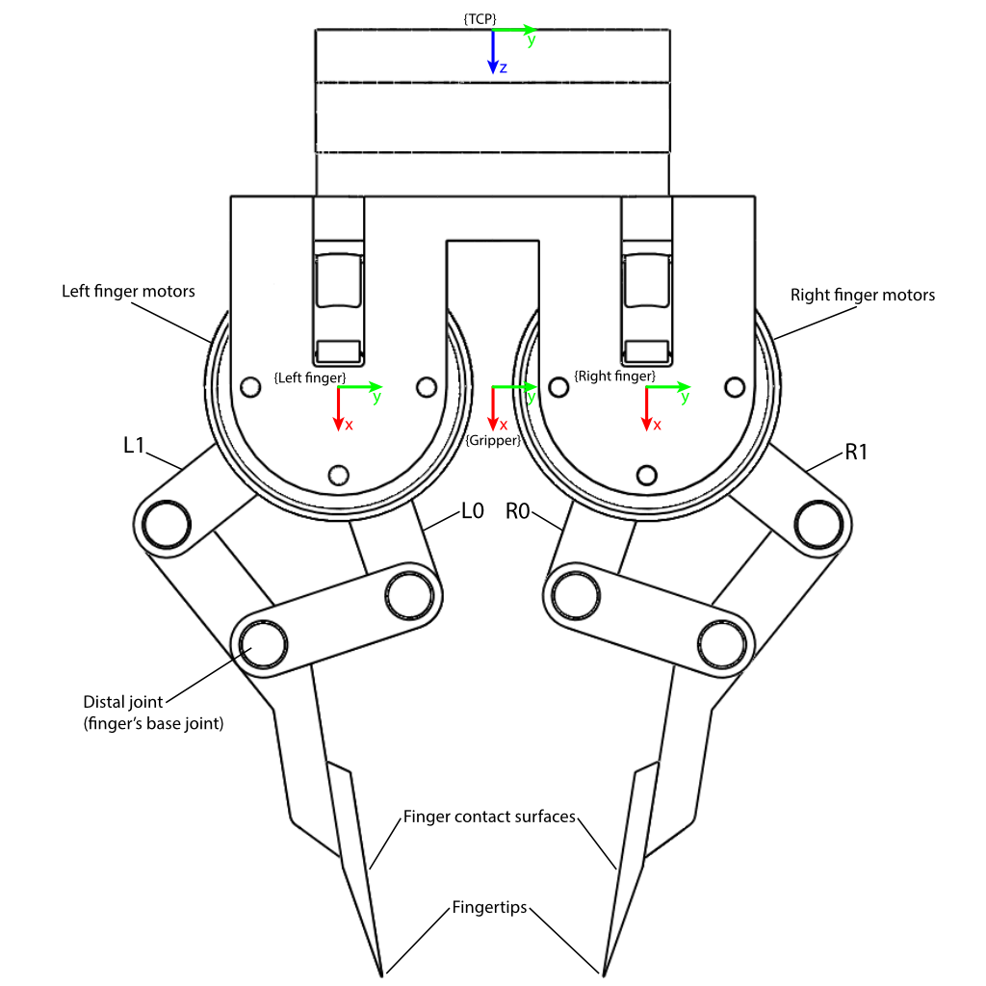
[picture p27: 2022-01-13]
images/ref_frame.png

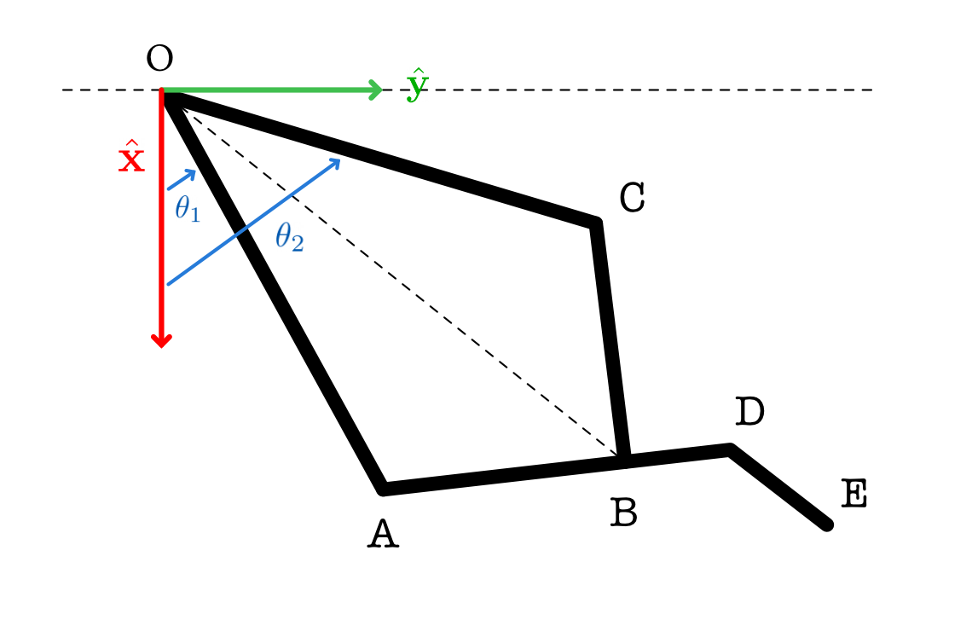
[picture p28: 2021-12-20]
images/theta1_theta2.png

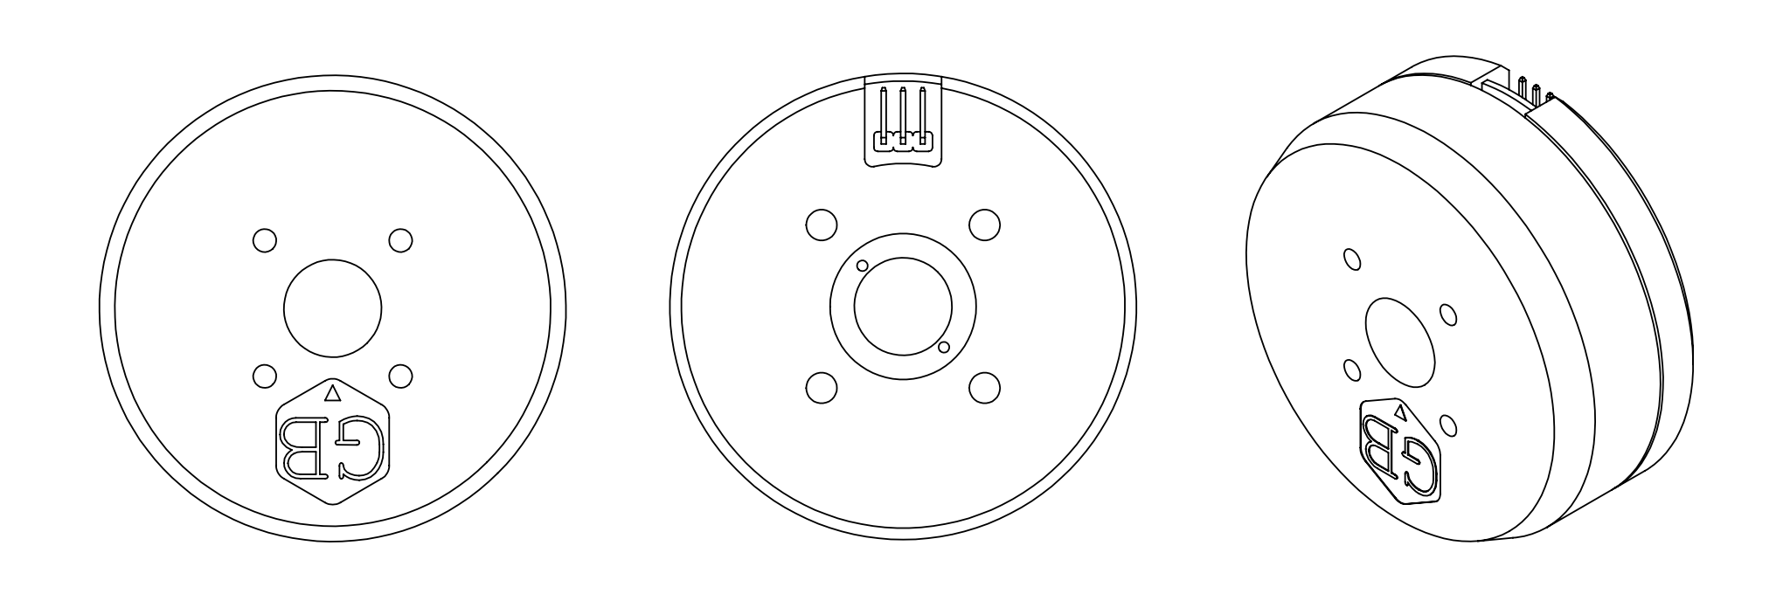
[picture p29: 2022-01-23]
images/motor_zero.png

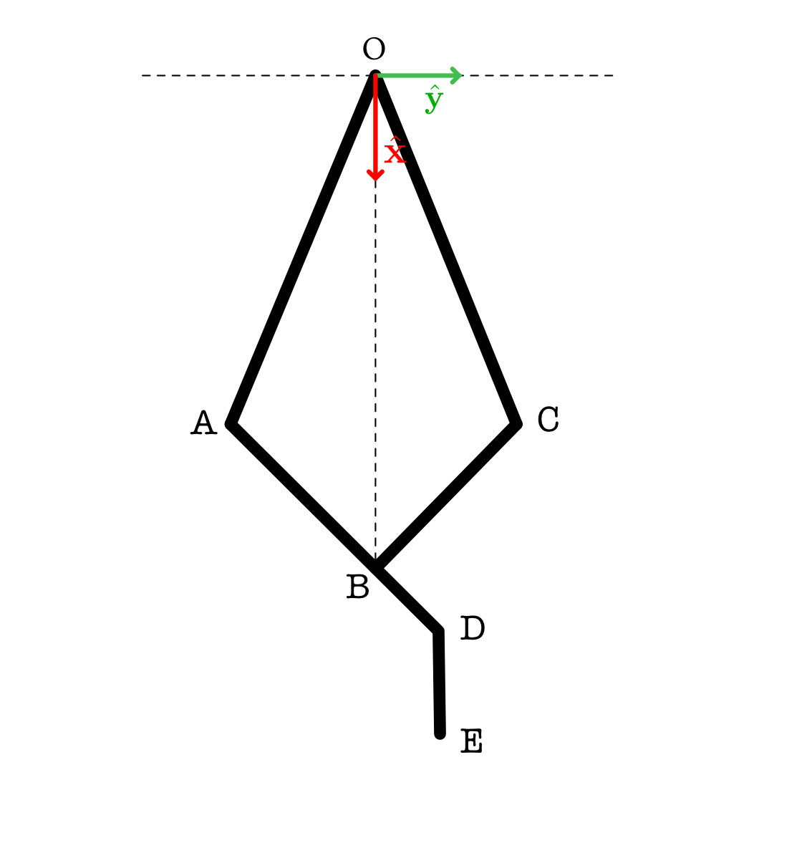
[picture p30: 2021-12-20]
images/linkage_geometry.png

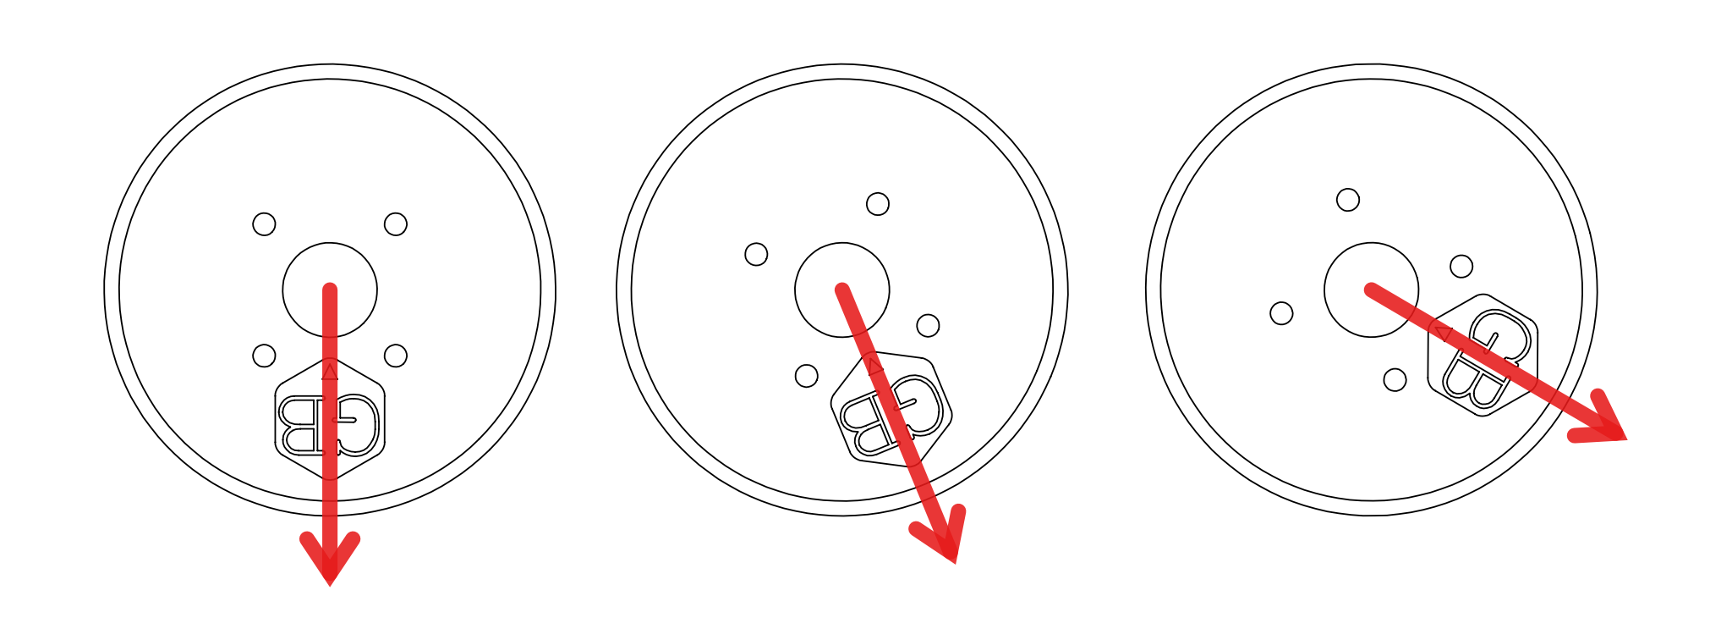
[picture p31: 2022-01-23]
images/rotor_dir.png

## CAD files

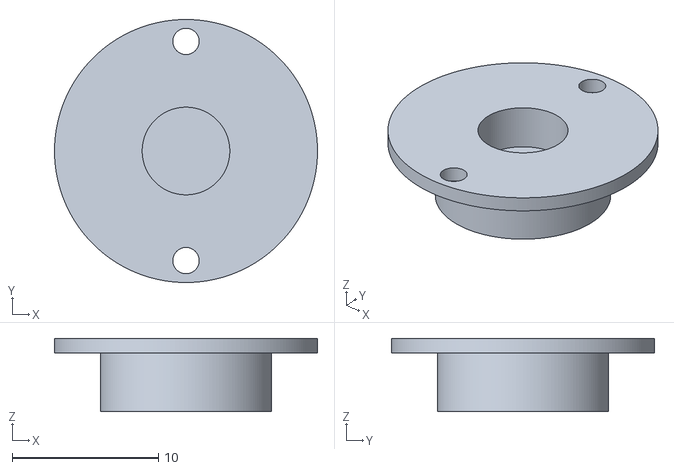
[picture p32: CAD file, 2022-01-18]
stl/magnet_holder.STL
18.0 x 18.0 x 5.00

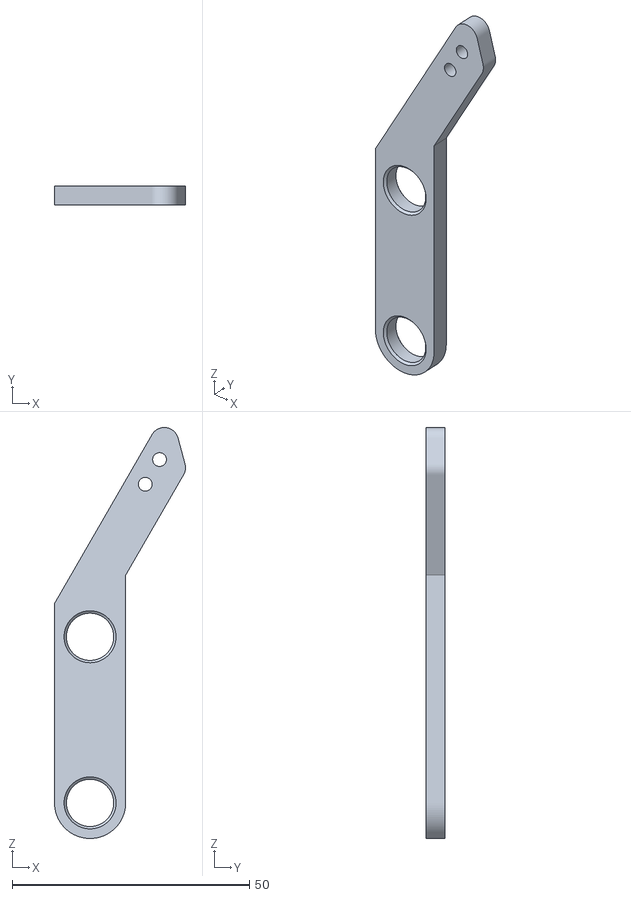
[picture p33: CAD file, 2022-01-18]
stl/distal_tip_link.STL
27.6 x 4.00 x 86.6

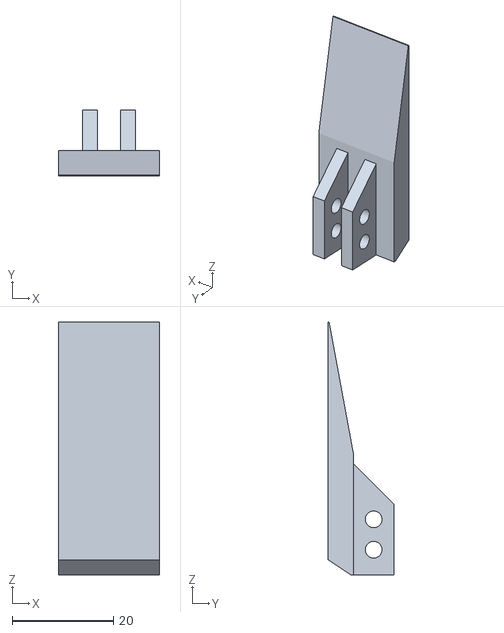
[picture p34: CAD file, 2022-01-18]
stl/finger_tip.STL
20.0 x 13.0 x 50.0

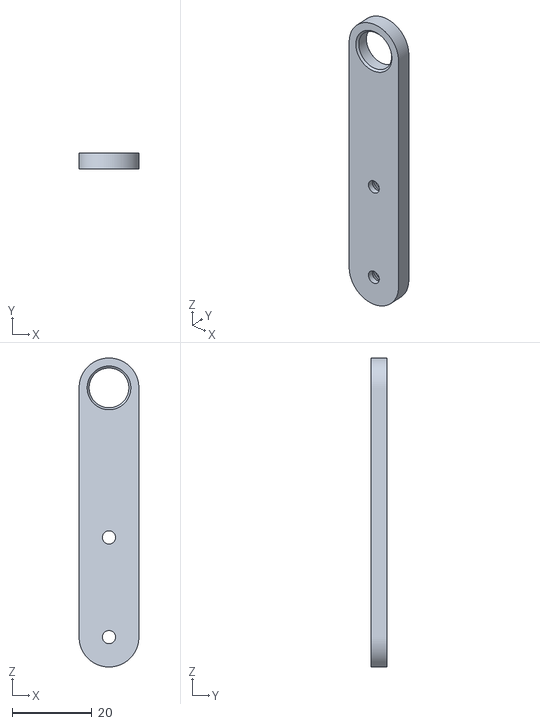
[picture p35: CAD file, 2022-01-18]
stl/proximal_link.STL
15.0 x 4.00 x 77.5

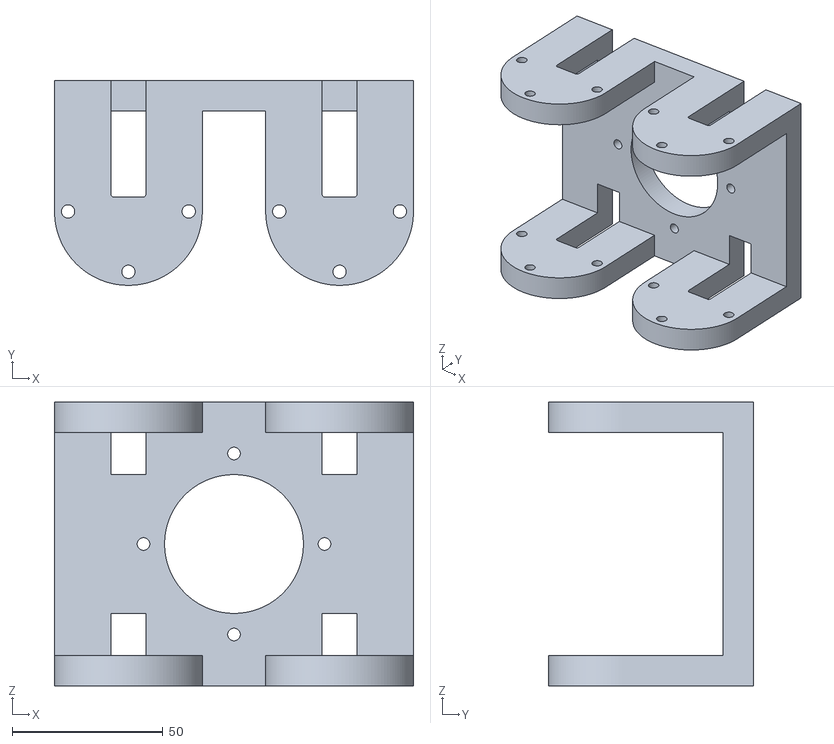
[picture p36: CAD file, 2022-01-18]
stl/gripper_shell.STL
119.0 x 67.8 x 94.0

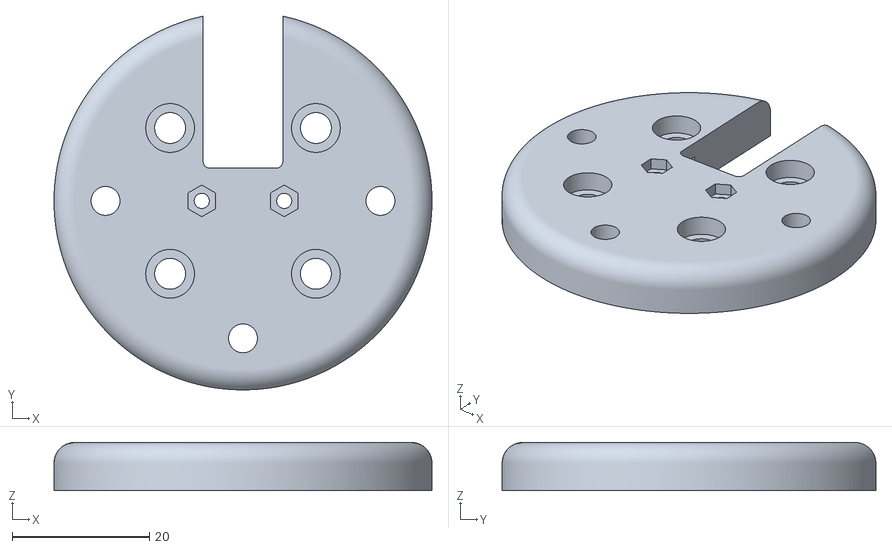
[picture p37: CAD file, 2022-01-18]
stl/motor_plate.STL
55.0 x 54.4 x 7.00

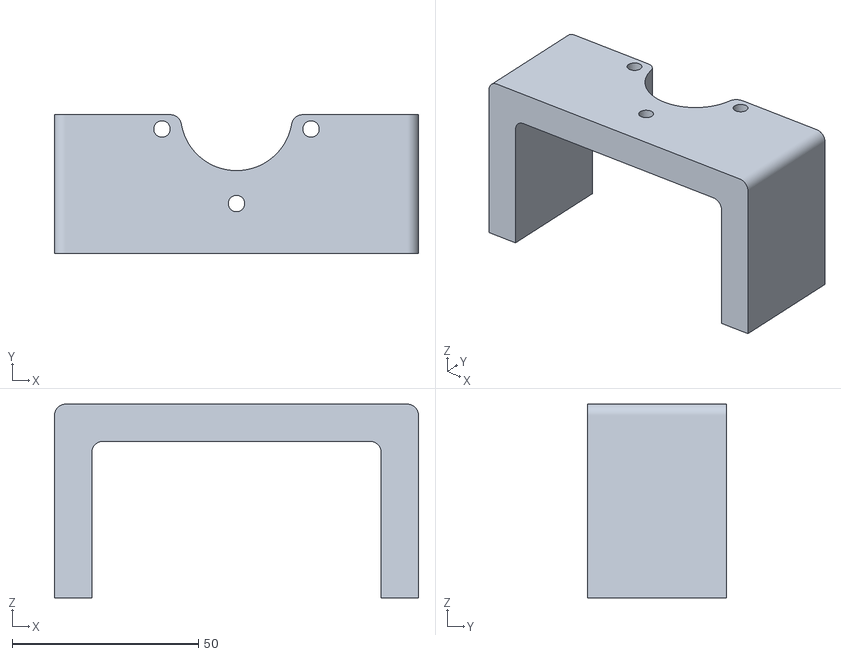
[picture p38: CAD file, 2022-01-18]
stl/calibration_stand.STL
97.7 x 37.2 x 52.0

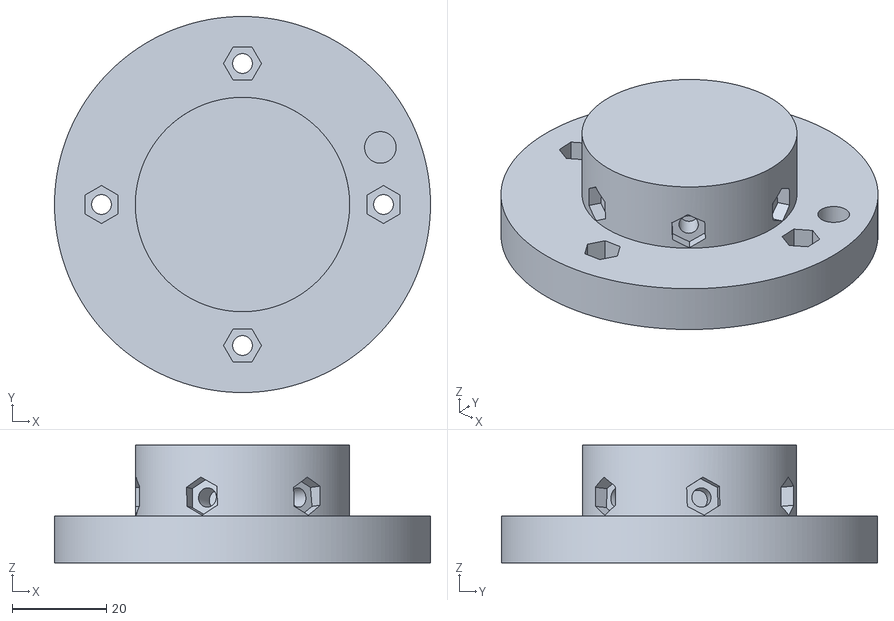
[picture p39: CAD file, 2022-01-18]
stl/coupler.STL
80.0 x 80.0 x 25.0

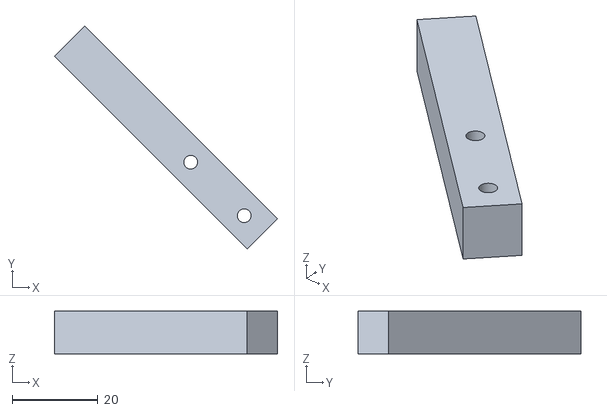
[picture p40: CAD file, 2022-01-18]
stl/calibration_arm.STL
52.1 x 52.1 x 10.0

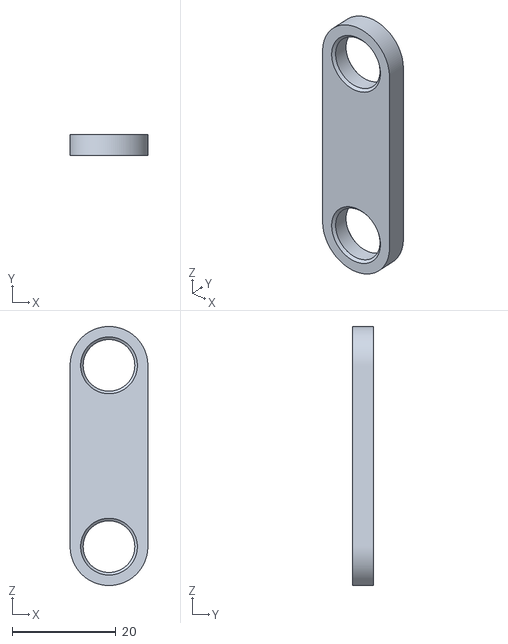
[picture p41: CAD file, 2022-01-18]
stl/distal_link.STL
15.0 x 4.00 x 50.0

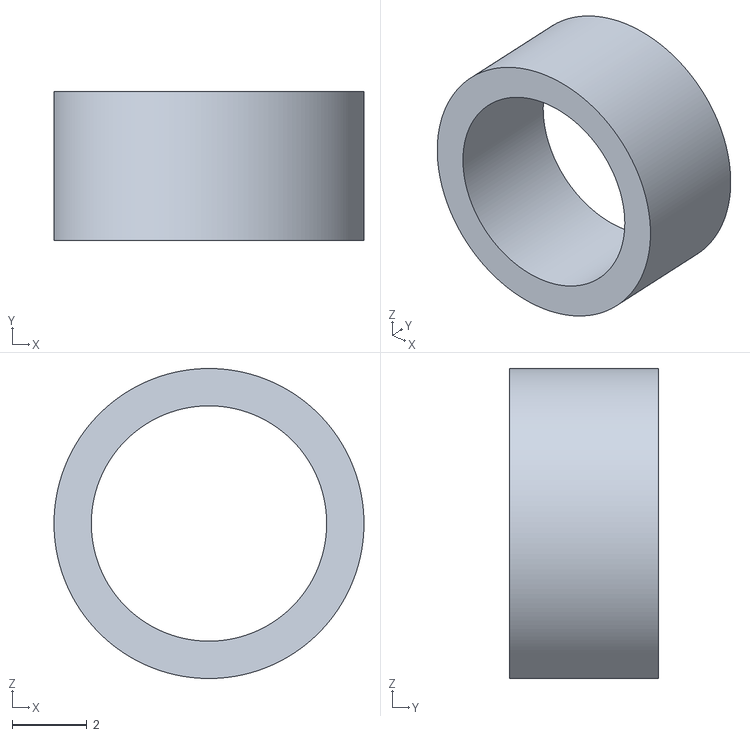
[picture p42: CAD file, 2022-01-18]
stl/bearing_spacer.STL
8.30 x 4.00 x 8.30

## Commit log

2022-01-09 update schematic and BOM
2022-01-10 add actuator module instruction
2022-01-10 add gripper shell, update image margins
2022-01-10 add linkage joint
2022-01-10 add finger assembly
2022-01-11 add calibration steps
2022-01-11 add gripper assembly
2022-01-11 add mounting
2022-01-11 add mounted
2022-01-12 add magnet image and wiring diagram
2022-01-12 add power wiring
2022-01-13 add schematics
2022-01-13 wiring guide added
2022-01-16 encoder calibration added
2022-01-18 add stl files
    [actuator_mount.STL, bearing_spacer.STL, calibration_arm.STL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]
2022-01-21 add photo of cable
2022-01-23 add motor frame definitions
2022-01-24 update gripper shell markings
2022-01-24 move definitions to the actuator section
2022-01-24 add photos for power connection
2022-02-04 smaller actuator mount figure
2022-02-04 fix naming issues
    [gripper_shell.STL]
2022-02-21 add power supply connection
2022-02-28 add mounting customization
2022-02-28 add custom finger tip
2022-03-01 update gripper geometry figure
